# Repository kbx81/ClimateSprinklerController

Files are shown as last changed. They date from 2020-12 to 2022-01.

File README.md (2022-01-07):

# kbx's Climate and Sprinkler Controller

Climate and Sprinkler Controller
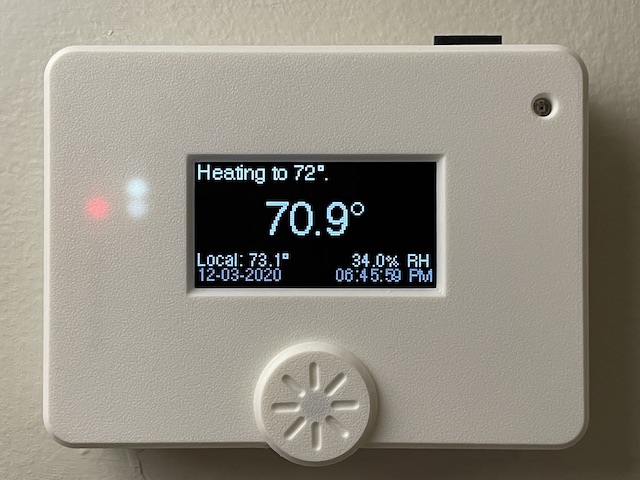
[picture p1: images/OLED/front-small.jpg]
Climate and Sprinkler Controller Climate and Sprinkler Controller - OLED


## A DIY Thermostat and/or Sprinkler (Valve) Controller

Here you'll find plans for an ESP32-based controller designed with [ESPHome](https://esphome.io) in mind. It is primarily designed for switching 24-volt AC circuits but it is flexible by design and should be adaptable to other types of electrical workloads.

In the [Preface](PREFACE.md) you will find background information about this project such as how it came to be and some personal thoughts and experiences I've had with home automation through the years.

In the [Hardware](HARDWARE.md) document you will find a general explanation of the theory of operation of a thermostat as well as a design overview of this device, some handy tips (should you choose to build one), construction, usage, and installation detail.

Finally, the [Hardware Detail](HARDWARE_DETAIL.md) document aims to explain why I did what I did -- design decisions, etc.

## Design Versions

At present there are two major "versions" of (iterations on?) the device -- a version that supports an OLED display such as the [SSD1325](https://www.adafruit.com/product/2674) and a version (well, actually three versions) that supports a Nextion touchscreen display. The project files for each can be found in its respective directory:
 - OLED versions:
   - [Version 2 (WROOM)](WROOM/)
   - [Version 3 (WROVER)](WROVER/)
 - Nextion versions:
   - [Nextion 3.5"](WROVER-Nextion3.5/) (contains no switching hardware!)
   - [Nextion 5"](WROVER-Nextion5/)
   - [Nextion 7"](WROVER-Nextion7/)

## PCB and BoMs

The schematic and PCB were drawn in [KiCAD](https://www.kicad.org). I had PCBs fabricated by [Elecrow](https://www.elecrow.com) but nearly any PCB fabricator should be able to manufacture these without any issues.

On [Octopart](https://octopart.com) I have posted a bill of materials (BoM) for each design version:
 - OLED versions:
   - [Version 2 (WROOM)](https://octopart.com/bom-tool/XvGbAePy)
   - [Version 3 (WROVER)](https://octopart.com/bom-tool/vZKpLnMD)
 - Nextion versions:
   - [Nextion 3.5"](https://octopart.com/bom-tool/dj6BW0gV) (contains no switching hardware!)
   - [Nextion 5"](https://octopart.com/bom-tool/kHZhyfjO)
   - [Nextion 7"](https://octopart.com/bom-tool/b5Lb00Zs)

### Important!

**Save money** by reading through the [build guide](HARDWARE.md) **before** you order any parts, as you likely _do not need **every** part in the linked BoMs!_ (For example, there are footprints multiple sensors on each PCB. You do not need all of the sensors!)

## ESPHome Configuration & Code

I've created a separate repository for my [ESPHome](https://esphome.io) [configurations](https://github.com/kbx81/esphome-configs); if you're looking for a starting point/example configuration, please have a look there.

## Legal stuff and License

Everything you see here is provided to you free of charge. You are free to use it however you please within the constraints of the license -- but you do so at your own risk. I accept absolutely no liability if you cause damage to your property, HVAC system, or any other hardware you choose to connect to this device.

The circuit schematics, PCBs and enclosures found here are licensed under the [Creative Commons Attribution-ShareAlike 4.0 International License](http://creativecommons.org/licenses/by-sa/4.0/).



_Thanks for visiting!_

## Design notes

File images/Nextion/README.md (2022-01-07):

# kbx's Climate and Sprinkler Controller

## Photo Gallery

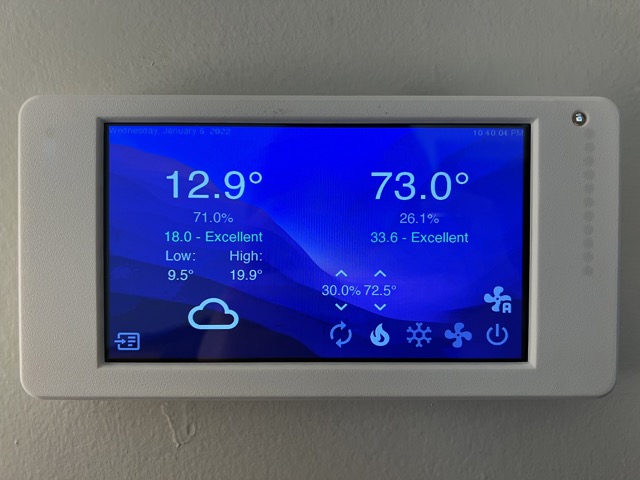
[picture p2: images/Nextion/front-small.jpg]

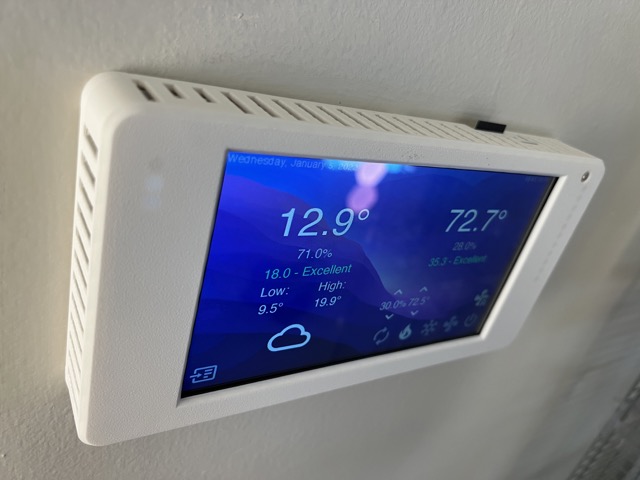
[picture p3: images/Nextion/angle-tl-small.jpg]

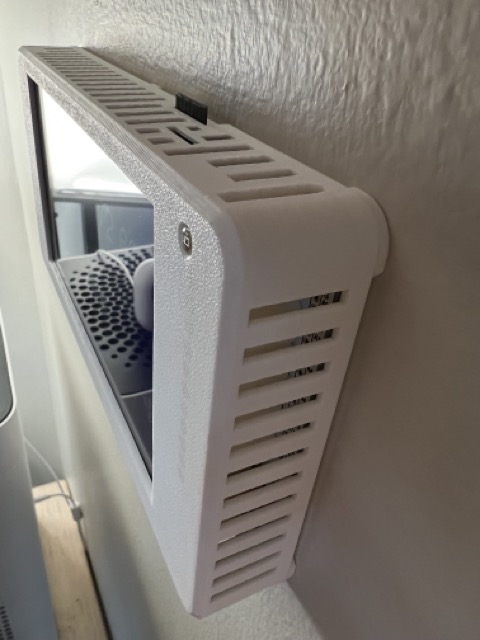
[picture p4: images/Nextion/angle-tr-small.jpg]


## Legal stuff and License

Everything you see here is provided to you free of charge. You are free to use it however you please within the constraints of the license -- but you do so at your own risk. I accept absolutely no liability if you cause damage to your property, HVAC system, or any other hardware you choose to connect to this device.

The circuit schematics, PCBs and enclosures found here are licensed under the
 [Creative Commons Attribution-ShareAlike 4.0 International License](http://creativecommons.org/licenses/by-sa/4.0/).



_Thanks for visiting!_

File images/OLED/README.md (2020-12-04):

# kbx's Climate and Sprinkler Controller

## Photo Gallery

Climate and Sprinkler Controller
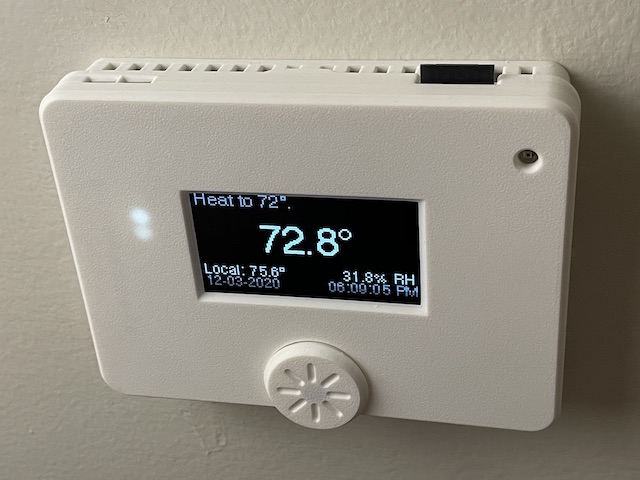
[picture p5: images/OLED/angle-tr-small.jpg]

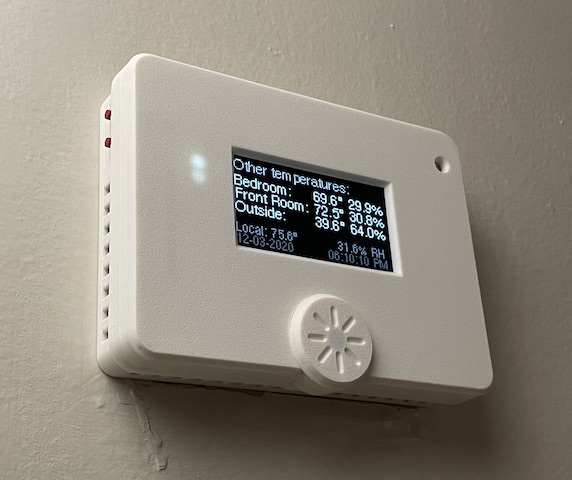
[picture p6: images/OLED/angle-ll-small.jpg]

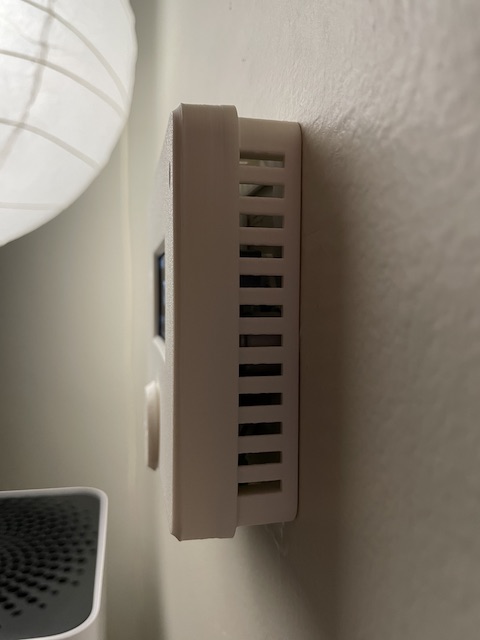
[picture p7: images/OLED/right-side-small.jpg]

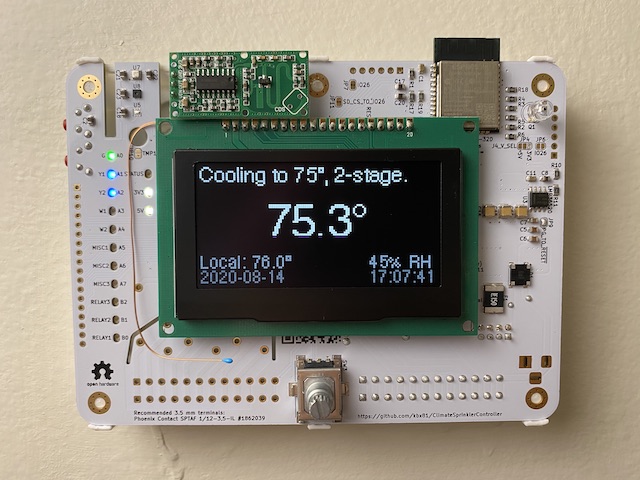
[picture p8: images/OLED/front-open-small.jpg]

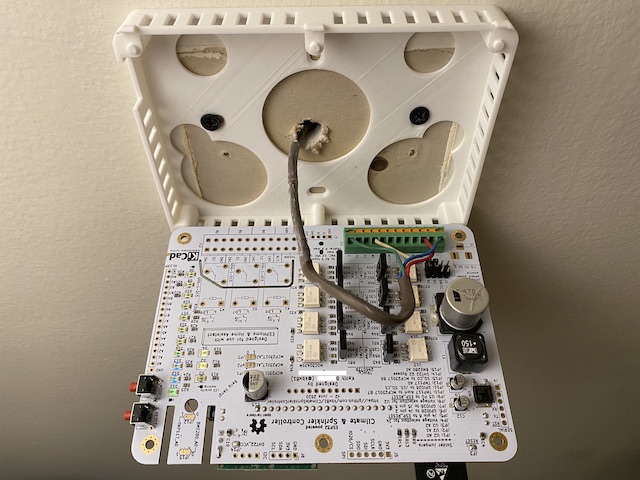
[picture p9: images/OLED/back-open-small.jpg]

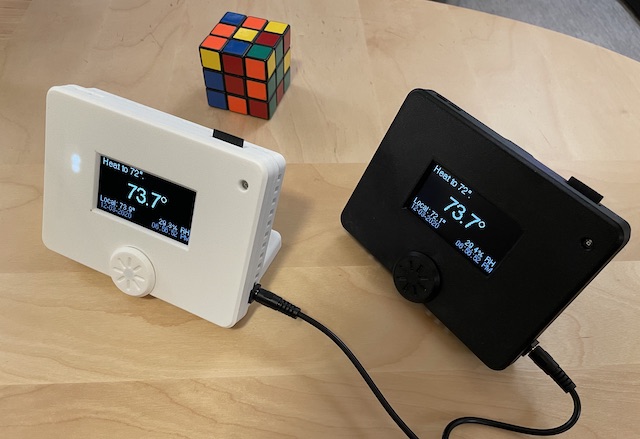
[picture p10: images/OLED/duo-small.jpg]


## Legal stuff and License

Everything you see here is provided to you free of charge. You are free to use it however you please within the constraints of the license -- but you do so at your own risk. I accept absolutely no liability if you cause damage to your property, HVAC system, or any other hardware you choose to connect to this device.

The circuit schematics, PCBs and enclosures found here are licensed under the
 [Creative Commons Attribution-ShareAlike 4.0 International License](http://creativecommons.org/licenses/by-sa/4.0/).



_Thanks for visiting!_

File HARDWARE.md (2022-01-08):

# kbx's Climate and Sprinkler Controller

Climate and Sprinkler Controller
Climate and Sprinkler Controller Climate and Sprinkler Controller - OLED

**If you want to dive right in to prepare your own build, skip down to the [Design Overview](#Design-Overview) section.**

This project started as a thermostat, but, application aside, it's just a processor with some combination of switches, sensors and/or a display connected to it. There are footprints on the PCBs for up to eleven switches and up to six sensors. It's primarily aimed at controlling 24 volt AC loads, although its relay(s) will allow switching a range DC voltages if required. Therefore, it should be able to operate more or less anything over a reasonably wide range of voltages and currents, from HVAC systems to electric sprinkler valves to security system hardware and variety of other things.

## The Basics

**If you are not planning to use this as a thermostat and/or are already familiar with HVAC system control and wiring, skip to the next section.**

### What is a Thermostat?

A thermostat is a switch. It is a switch that happens to be controlled by temperature. The switch is either on or it is off.

Yup. That's it. It's literally just a temperature controlled switch -- I'm not over-simplifying. That's really all it is.

If your thermostat happens to control your heating system, it does exactly two things:
 1. When the temperature drops below the temperature you set on it, the switch turns on.
 1. When the temperature rises above the temperature you set on it, the switch turns off.

You thought it was more complicated than that? Sorry if I've disappointed you! That's really about it. Don't believe me? Here's a [lovely video](https://youtu.be/ZZC0SP02PqY) if you'd like a closer look!

Ok, ok..._some modern systems_ allow control that is more advanced than just that. Still, it's reasonably safe to say that most (residential) systems that are either more than about ten years old or are "small" (for example, those found in single or two bedroom homes/apartments that just don't require a lot of power to heat or cool them) do little more than that. For larger homes or (commercial) buildings, the control may be more complex and, as such, may require a more complex controller. Those are probably out of the scope of what's here.

### Getting Connected

I'm not going to reinvent the wheel here. There are a number of guides that explain [thermostat wiring](https://lmgtfy.com/?q=thermostat+wiring) if you are interested in learning more. Where I live, forced-air systems that both heat and cool are most common and, as such, most of my experience is with them. To quickly summarize, our thermostats are usually connected to these systems with four to five wires:
 - `R`: a red wire, which is "live" with 24 volts AC
 - `G`: a green wire, which controls the system's main blower fan. The thermostat internally shorts this to the `R` wire to activate the fan.
 - `W`: a white wire, which controls the system's heating capability. The thermostat internally shorts this to the `R` wire to activate heating.
 - `Y`: a yellow wire, which controls the system's cooling capability. The thermostat internally shorts this to the `R` wire to activate cooling.
 - `C`: a blue wire, which provides the return path from the `R` wire (above) to complete the (24 volt AC) circuit. **This is the wire that is usually missing and brings about the "not enough wires" problem I described in the [Preface](PREFACE.md).** Without this wire, there is no reliable way for the thermostat to draw power from the system and consequently it will not work because it simply has no power. This is the reason thermostats with batteries in them are so common here now -- their old mechanical predecessors simply didn't require power to function as modern, electronic thermostats do. As a cost-saving measure, installers often ran cables that did not include this wire.

### Even More Connected

More modern systems may have additional wires, such as a `W2` (second stage heating), `Y2` (second stage cooling), `RH` (`R` for heating system), or `RC` (`R` for cooling system). These are arguably only found in large(r) homes or buildings where extra cooling or heating capacity might be needed to adjust the indoor temperature when the outdoor temperature is more extreme. Still, the controller you've found here can support these particular connections (and then some) if they are available!

In addition to heating and cooling, some systems have the ability to humidify and/or dehumidify. Here, it is common to use the air conditioning system for dehumidification, while humidification is accomplished with a separate unit when needed (typically in the winter season). If available, you can connect (de)humidifiers to any of this controller's relays or "MISCx" TRIACs -- confirm the unit's power requirements before doing so!

## Design Overview

When I design devices such as this, I tend to focus on flexibility -- cost is usually an afterthought. This device is no exception; it can be built at least three different ways...but probably isn't the cheapest possible DIY option.

There are five key components:
 - Power supply
 - Processor (ESP32)
 - Sensors
 - Display
 - I/O Expander and switching hardware:
   - TRIACs, opto-isolators, snubber circuits
   - Relays, FETs, kick-back diodes

I can probably go without saying that the power supply and processor are always required if you want it to function at all. While (the) sensor(s) may be omitted, this is not recommended if it is to be used as a climate control device (I'll explain why later). With these items in mind, it is otherwise possible to omit:
 - the display, or
 - the I/O expander and switching hardware

Any combination of TRIACs and/or relays may be installed; in other words, it is not necessary to install _all_ relays and/or _all_ TRIACs. Just install the number of TRIACs and/or relays that you need for your use case. For example, if the application requires a single DC circuit and two AC circuits, only a single relay and two TRIACs could be installed. As an alternative in this situation, three relays could be used (and no TRIACs). This is entirely at the discretion of the builder. (Note that a benefit of the TRIACs is that they are not subject to contact wear as relays are -- in theory, they should last forever. Relay contacts wear out and will stop working after some time.)

Based on the above two build configurations, I've come to think of these devices in two ways:
 - A `controller`, which is a unit that has the switching hardware and may or may not have a display and encoder
 - A `satellite`, which has a display and encoder but no switching hardware

Both build configurations have at least one sensor.

I use a couple `satellite` units to monitor and report to Home Assistant the temperature in remote (with respect to the wired-in `controller` build) rooms. This data can then be used to guide the `controller` that is physically connected to the HVAC system. It's easy to aggregate the data from any number of `satellite` units and, with the right automations in place, use it to control the system. In addition, `satellite` units can provide alternate points of control for the system; for example, put one next to your bed and you could adjust the temperature without using your smartphone or voice control (and potentially waking up your SO in the process).

`Controller` units are builds that have (some) switching hardware but may or may not have a display. If built with a display, you can probably mount it on the wall as a direct replacement for your existing thermostat. With no display, the controller can still control your HVAC system (or whatever else you've wired up to it), you just won't be able to interact with it locally (at least, not easily). While building it this way might seem like a silly idea, _this is the solution to the "not enough wires" problem._

### Solving the "Not Enough Wires" Problem

_How does building it without a display solve the "not enough wires problem"?_

Imagine, for a moment, that your HVAC system is located in the basement of your house. Your thermostat is installed on a wall on the main floor. The cable to your thermostat from your HVAC system runs up, through the floor, around a corner, down the hall and finally up the wall to where your thermostat is mounted. You need five wires to install your new thermostat, but the system installer ran a cable that has only four wires. What do you do?

(At this point, I can assure you that your HVAC professional will install a small white plastic box with a tiny LCD on it. It will require a battery (or two) that you'll have to change periodically, probably once or twice a year. The battery will always fail at an inopportune time.)

By building one of these as a `controller` (and perhaps without a display and encoder), you can:
 1. Mount your `controller` (very) near your HVAC system -- for example, on the wall directly behind it...or hanging on the side of it
 1. Get a short cable--say, one to two yards/meters or so--that _does_ have enough wires (or you could recycle a couple pieces of the cable you'll disconnect in the next step!)
 1. Disconnect the original cable from your HVAC system to your old thermostat, then
 1. Connect the new short cable from your HVAC system to the new `controller` that's now right next to your system.

What you have now is a switching device that can still _tell your HVAC system what to do_ -- you'll just need to feed it data from remote sensors (in this example, sensors that are located upstairs). These remote sensors could be the "satellite" units I described above -- or they could be something even more simple, such as [these sensor boards](https://github.com/kbx81/TempHumSensWithESP01). There also exists a super cheap [DHT22 + ESP-01 module](https://www.amazon.com/gp/product/B07L6CYFT9/)...although, in practice, I _really_ don't recommend DHT modules for this application -- they're too inconsistent. It's up to you!

So, to summarize:
 - The `controller` is installed (very) near your HVAC system and is connected to it with a short, easily-installed cable that _has enough wires_.
 - `Satellite` sensors located in areas to be climate controlled report data to Home Assistant.
 - (An) automation(s) in Home Assistant parse and feed this data back to the `controller` so that it can control your system as appropriate.

Ok, ok...I admit, it's more of a workaround than a "real solution". Even so, it works great!

### But What If...

I'm going to assume that, since you're here and are reading this, you're at least somewhat technically inclined and are asking "What if my Home Assistant goes down??? What if my Wi-Fi goes down??? This won't work then so I can't use it!" You may recall that, above, I stated: "While (the) sensor(s) may be omitted, this is not recommended if it is to be used as a climate control device." In the [ESPHome](https://esphome.io) [configuration](https://github.com/kbx81/esphome-configs/blob/master/CSC.md) that I built for my devices, two events are monitored:
 1. The API connection state (Am I connected to [Home Assistant](https://www.home-assistant.io)?)
 1. The time since the [ESPHome](https://esphome.io) [template sensor](https://esphome.io/components/sensor/template.html) was last updated (by (an automation in) [Home Assistant](https://www.home-assistant.io))

There is a timer for each of these two events; each event's respective timer is reset each time the event occurs (such a mechanism is also often called a "watchdog"). If the device either 1. loses its connection to the [Home Assistant](https://www.home-assistant.io) API ([Home Assistant](https://www.home-assistant.io) is down, Wi-Fi is down) or 2. does not receive an update to the [template sensor](https://esphome.io/components/sensor/template.html) (your automation that updates it broke or otherwise stopped running), after a duration of your choosing, it will stop using the [template sensor](https://esphome.io/components/sensor/template.html) and switch to using its local sensor (BME280/BME680/SHTC3/TMP117/DHT22/Thermistor...note that in my [configurations](https://github.com/kbx81/esphome-configs/blob/master/CSC.md) I revert to using the BME680 in this case). While the data from its local sensor(s) won't necessarily be consistent with the sensors located in the areas of interest, it _will_ provide the controller with _some_ data so that it can continue to function on some level. It may not be ideal, but it can keep the system from becoming totally useless (and, as such, your house doesn't freeze/turn into a sauna).

It's not a perfect solution to the original problem and I'm sure that it won't work for everybody. Still, it should offer a level of flexibility that I think many home automation enthusiasts can work with. My experience has proven that [Home Assistant](https://www.home-assistant.io), [ESPHome](https://esphome.io) and my Wi-Fi/home network are extremely reliable and that they can handle this task with no trouble at all. They break _only when I break them_.

## I Want (to Build) One

Awesome! Read on for build-related information, tips, etc.

### Before You Build

If you've read through the previous section, you may have already begun thinking about how you'd like to build yours. _But,_ just in case you skipped that part, I'll outline the key points you need to consider here:
 1. How many units do you need? Are you simply replacing a single existing thermostat or do you desire/plan to extend the capabilities of your system, as well?
 1. How many control channels do you need for your intended application? For example, if you're only controlling a heating system, you likely only need a single channel. If you have a more complex system that can (for example) heat, cool, fan and humidify, you need at least four channels/circuits. This determines how many TRIACs and/or relays you will need.
 1. If you are replacing an existing thermostat, _do you have enough wires?_ (My favorite problem!) If not, you may want to build a `controller` version as well as a `satellite` version (see above). As an alternative, you could build a complete version and power it with an external source through the barrel jack on the side. I recommended _not_ installing the barrel jack if your HVAC system will provide power through the `R` and `C` wires.
 1. Which sensor(s) do you wish to use? Are you comfortable soldering tiny parts such as the BME280, BME680, SHTC3 or TMP117 (you need a hot air station or (toaster) oven for these!)? If not, is a DHT22 or thermistor accurate/consistent enough for your liking/needs? If not, consider a BME280, BME680, SHTC3 or TMP117 module from [Adafruit](https://www.adafruit.com/product/2652) or [Sparkfun](https://www.sparkfun.com/products/13676)! They can be plugged into one of the headers along the edges of the board. (My personal favorite is the BME680.)
 1. Do you want/need a display? If so, which display do you want to use? On the v2 and v3 boards there are headers for two different displays -- the [SSD1325](https://www.adafruit.com/product/2674) (grayscale, big) and the [SSD1351](https://www.adafruit.com/product/1431) (color, not big). If you prefer a touchscreen, there are three different boards to match three different Nextion display sizes. I highly recommend the [Intelligent series](https://nextion.tech/intelligent-series-introduction/) or, as a less-expensive alternative, the [Enhanced series](https://nextion.tech/enhanced-series-introduction/). (I'd avoid the Basic series altogether -- they're rather sluggish.) My personal favorites are the Intelligent series models `NX8048P070-011C` (7") or the `NX8048P050-011C` (5"); I've also built [HMI configurations](https://github.com/kbx81/esphome-configs/tree/master/nextion/CSC/climate) for the Enhanced series `NX4832K035` (3.5"), `NX8048K050` (5"), and `NX8048K070` (7"). **Note that the 3.5" board does not include any switching hardware -- as such, it can only function as a satellite.**
 1. Do you want the display to be motion-activated? This is especially important if it is an OLED-type of display -- they have a relatively short lifespan and can burn in! I used an [RCWL-0516 module](https://www.amazon.com/gp/product/B07MTWZDQZ/) to accomplish this, although a PIR sensor is suitable, as well. There is a header on each board for this purpose. (Pro-tip: I've installed a short jumper cable with a dupont-style connector and mounted the [RCWL-0516 module](https://www.amazon.com/gp/product/B07MTWZDQZ/) into the back side of the front cover of the enclosure. This arrangement distances it from the PCB which allows it to function more reliably.)

Once you have the PCBs and parts in-hand, you're ready to begin building!

### Construction

The bill of materials (BoM) for each version of the board contains not only the list of parts, but also the component references -- it can be used to determine what parts go where on the PCB. This (as well as some patience and a steady hand) should be everything you need to complete assembly.

Note that the PCB is designed in a way that it has parts on both sides. Examine it carefully and **observe that one side has only small parts** while the other side has several larger parts. **I highly recommend starting with the side of the board that has only small parts on it.** This side has no "heavy" or otherwise particularly large parts on it, so assembling it first will make assembling the side with the larger parts later on much easier. I use and recommend a stencil with solder paste and a hot air soldering station, so having a board that doesn't wobble (much) when it's on the desk is important.

As you're assembling, you'll notice a number of solder jumpers on the board. This is a good point to discuss what they do so you can determine which ones you should bridge and how.

#### Solder Jumpers: v2/WROOM

- JP1 to JP3: U2 (MCP23017) I2C address selection. These are used to modify the I2C address of the MCP23017. (*See the note below.)
- JP4: Voltage selection for pin 3 of J4. Not connected by default; create a solder bridge to the voltage of your choosing if connecting an external device. **Not required for ESP32 programming.**
- JP5: J4 pin 6 to ~ESP_RESET aka EN -- connects through C4 to the ~RESET aka EN line of the ESP32 to allow resetting from a connected serial adapter.
- JP6: Connects the ESP32's GPIO26 pin to J4 pin 2.
- JP7: Connects the ESP32's GPIO26 pin to J5 pin 6.
- JP8: Voltage selection for U2 (MCP23017). This IC can operate with either 3.3 or 5 volts. _Use 5 volts with caution_ as the interrupt lines may put 5 volts onto the ESP32's GPIO 36 and/or 39 pins! This may cause undefined behavior and/or damage the ESP32. If using 5 volts, these pins must be configured to open drain mode on the MCP23017.
- JP9: U3 (LMR36520) PG to ~ESP_RESET aka EN -- allows the LMR36520 to hold the ESP32 in "reset" state until the power from the buck converter has stabilized.
- JP10: TMP117 Alert to MCP23017 B7. Not used if the TMP117 is not installed.
- JP11: ESP32 GPIO26 to J10, SD_CS pin -- may be used if the [SSD1351](https://www.adafruit.com/product/1431) is installed and the SD card is to be used.
- JP12: TMP117 A0 -- allows changing the I2C address of the TMP117. (*See the note below.)
- JP13: SD_CD to MCP23017 B6 pin -- may be used if the [SSD1351](https://www.adafruit.com/product/1431) is installed and the SD card is to be used.
- JP14: DHT22 Q2 Bypass. Shorts the drain and source pins of Q2. This transistor can be used to power-cycle the DHT22 if required by the application (they sometimes stop responding). Not used if the DHT22 is not installed. Note that this transistor could also be used to drive an LED, if required.
- JP15: BME280 A0 -- allows changing the I2C address of the BME280. (*See the note below.)

#### Solder Jumpers: v3/WROVER

- JP1 to JP3: U2 (MCP23017) I2C address selection. These are used to modify the I2C address of the MCP23017. (*See the note below.)
- JP4: MCP23017 Interrupt B output to GPI39
- JP5: MCP23017 Interrupt A output to GPI36
- JP6: Voltage selection for pin 3 of J4. Not connected by default; create a solder bridge to the voltage of your choosing if connecting an external device. **Not required for ESP32 programming.**
- JP7: J4 pin 6 to ~ESP_RESET aka EN -- connects through C4 to the ~RESET aka EN line of the ESP32 to allow resetting from a connected serial adapter.
- JP8: Connects the ESP32's GPIO26 pin to J4 pin 2.
- JP9: Connects the ESP32's GPIO26 pin to J5 pin 6.
- JP10: Voltage selection for U2 (MCP23017). This IC can operate with either 3.3 or 5 volts. _Use 5 volts with caution_ as the interrupt lines may put 5 volts onto the ESP32's GPIO 36 and/or 39 pins! This may cause undefined behavior and/or damage the ESP32. If using 5 volts, these pins must be configured to open drain mode on the MCP23017.
- JP11: U3 (LMR36520) PG to ~ESP_RESET aka EN -- allows the LMR36520 to hold the ESP32 in "reset" state until the power from the buck converter has stabilized.
- JP12: TMP117 Alert to MCP23017 B7. Not used if the TMP117 is not installed.
- JP13: ESP32 GPIO26 to J10, SD_CS pin -- may be used if the [SSD1351](https://www.adafruit.com/product/1431) is installed and the SD card is to be used.
- JP14: TMP117 A0 -- allows changing the I2C address of the TMP117. (*See the note below.)
- JP15: SD_CD to MCP23017 B6 pin -- may be used if the [SSD1351](https://www.adafruit.com/product/1431) is installed and the SD card is to be used.
- JP16: BME280 A0 -- allows changing the I2C address of the BME280. (*See the note below.)

#### Solder Jumpers: Nextion 5" and 7"

- JP1 to JP3: U2 (MCP23017) I2C address selection. These are used to modify the I2C address of the MCP23017. (*See the note below.)
- JP4: MCP23017 Interrupt B output to GPI39
- JP5: MCP23017 Interrupt A output to GPI36
- JP6: Nextion power switch (U4) bypass
- JP7: Voltage selection for U2 (MCP23017). This IC can operate with either 3.3 or 5 volts. _Use 5 volts with caution_ as the interrupt lines may put 5 volts onto the ESP32's GPIO 36 and/or 39 pins! This may cause undefined behavior and/or damage the ESP32. If using 5 volts, these pins must be configured to open drain mode on the MCP23017.
- JP8: GPIO26/~RTS~ to J5 pin 2
- JP9: Voltage selection for J5
- JP10: U5 (LMR36520) PG to ~ESP_RESET aka EN -- allows the LMR36520 to hold the ESP32 in "reset" state until the power from the buck converter has stabilized. **Do not connect if powering from USB.**
- JP11: Auto-reset to ESP32 EN (allows the FT232 to reset ESP32)
- JP12: Auto-reset to ESP32 GPIO0 (allows the FT232 to invoke the ESP32's bootloader as required)
- JP13: GPIO15 to J6 pin 6 (to be used as SPI CS)
- JP14: BME680 A0 (*See the note below.)
- JP15: BME280 A0 (*See the note below.)
- JP16: TMP117 Alert to MCP23017 B7
- JP17: TMP117 A0 (*See the note below.)

#### Solder Jumpers: Nextion 3.5"

- JP1: GPIO26/~RTS~ to J4 pin 2
- JP2: Voltage selection for J4
- JP3: GPIO15 to J5 pin 6 (to be used as SPI CS)
- JP4: U3 (LMR36520) PG to ~ESP_RESET aka EN -- allows the LMR36520 to hold the ESP32 in "reset" state until the power from the buck converter has stabilized. **Do not connect if powering from USB.**
- JP5: VCC selection -- connects VCC to buck converter output or directly to barrel connector (J2)
- JP6: Auto-reset to ESP32 EN (allows the FT232 to reset ESP32)
- JP7: Auto-reset to ESP32 GPIO0 (allows the FT232 to invoke the ESP32's bootloader as required)
- JP8: Nextion power switch (U4) bypass
- JP9: TMP117 Alert to GPI36
- JP10: TMP117 A0 (*See the note below.)
- JP11: BME680 A0 (*See the note below.)
- JP12: BME280 A0 (*See the note below.)

*Note: This jumper is shorted to `0` by default; if you wish to modify it, use a razor knife to cut the trace between the center and `0` pads on the board and then create a solder bridge between the center pad and the `1` pad. Use your DMM to confirm proper/expected conductivity!

After you're done assembling but **before powering it on for the first time**, always check for shorts -- particularly across power tracks. I use my DMM to measure between ground, the 3.3 volt and 5 volt rails to be sure they are not shorted together. If any of them are, you'll need to carefully check your soldering work and look for solder bridges. If there are no shorts, it's probably safe to power it on and load the firmware image onto the ESP32.

#### One More Thing!

There is a header labeled `POWER SEL` (either `J2` or `J3`) to the lower left of the PCB. This header **must** be fitted with a jumper to select where the board should draw power from. There are up to four options: one of three possible AC circuits (`RC`/`C`, `RH`/`C`, or `RMISC`/`C`) as well as the barrel jack (`J1` or `J2`). In the event that your HVAC system does not have separate/individual `RC` and/or `RH` wires, it is possible to jumper them together by placing jumpers on _both_ `RC` _and_ `RH`. This effectively turns them into a single `R` terminal. `RMISC` may also be added into this mix, as needed. This may be done if only a single `R` wire is available/connected.

Note that on all except the Nextion 3.5" board the barrel jack may be an AC or DC source and it is not polarity sensitive because of the bridge rectifier. It must provide a minimum of 7.5 volts and a maximum of 40 volts DC or 30 volts AC (because RMS, yada yada). A common 12-volt DC power brick will likely work best if the board is to be powered this way. Depending on the input voltage and connected peripherals/accessories, its current requirement will vary. Even with a low input voltage (say, nine volts or so) it shouldn't need more than about 250 mA unless you've attached some extra hardware (sensors, LEDs, etc.) -- keep in mind, however, that the Nextion versions are slightly more power-hungry, depending on the display size. Even so, because of the buck converter, a higher voltage source will mean a lower current draw. Ideally the rating of the polyfuse `F1` should be adjusted accordingly, although the specified value should be suitable for most situations.

**Note that if, on the Nextion 3.5" board, `JP5` is set to bypass the buck converter, _only_ a 5-volt DC source may be used!**

For safety reasons, do not connect more than one power source at a time.

### Initial Firmware Flashing

After confirming that your new boards are electrically safe to power on (you checked everything as I suggested above, right?!), the ESP32 needs to have [ESPHome](https://esphome.io) installed ("flashed") onto it.

You'll need to either build an [ESPHome](https://esphome.io) configuration of your own or [start with mine](https://github.com/kbx81/esphome-configs/blob/master/CSC.md) and tweak them to your liking.

The Nextion versions of the boards have an FT232 USB-to-serial IC on the board; I definitely recommended using this for installing the firmware. Bridge both of the "Auto-reset" jumpers on these boards for the best experience.

If you're not using one of the Nextion versions of the boards or you did not place the FT232, you'll need to manually invoke the ESP32's bootloader to enable flashing. Hold down the "Mode" pushbutton (which is connected to the ESP32's GPIO 0 pin) as you either power it on or tap the adjacent reset button, then release the "Mode" button. With the bootloader invoked, you can use the pin header labeled "SERIAL" (`J4` or `J5`) to connect your serial adapter and flash the ESP32. There are plenty of guides on flashing ESP32s out on the web, so I'm not going to reinvent the wheel here. If you are having difficulty doing so, however, use your DMM and check for shorts across the transmit (TX) and receive (RX) lines. It's possible one or the other is shorted to ground, Vcc, or another adjacent pin or track. In some cases, it may be necessary to hold down the encoder button (connected to GPIO 2) _as well as_ the "Mode" button (GPIO 0) to properly invoke the bootloader -- try this first if you're having any trouble.

Once you've installed the firmware onto the ESP32, you're ready to begin using your Climate and Sprinkler Controller(s)! If you made it this far, nice work!

## Installation and Usage

Physically installing the controller is pretty straight forward -- the terminal strips are labeled just like a typical thermostat. _Power off your HVAC system before (dis)connecting anything!_ Connect the wires as you would any other thermostat and you should be ready to go. The [ESPHome](https://esphome.io) [configurations](https://github.com/kbx81/esphome-configs/blob/master/CSC.md) I've created aim to function just like a "real thermostat".

Once all the little wires are connected, turn your HVAC system's power back on and your new controller should start up. Please see [this document](https://github.com/kbx81/esphome-configs/blob/master/CSC.md#thermostat-user-interface-ui) for an explanation of the device's user-interface (UI).

To test the thermostat:

- If your system supports heating, set the thermostat mode to either `Auto` or `Heat` mode and turn the temperature up to a value at least one degree above the currently displayed room/air temperature. Heating should commence.
- If your system supports cooling, set the thermostat mode to either `Auto` or `Cool` mode and turn the temperature down to a value at least one degree below the currently displayed room/air temperature. Cooling should commence.

### Important Note!

The [ESPHome](https://esphome.io) [configurations](https://github.com/kbx81/esphome-configs/blob/master/CSC.md) I've created use the [thermostat's](https://esphome.io/components/climate/thermostat.html) delay timers to prevent the physical outputs (TRIACs, in this case) from changing states too quickly. For example, AC compressors are sensitive to being switched on/off rapidly (this is called "short cycling"). Because of this, you may find that cooling/heating will not stop despite that the temperature has been reset to a value that triggers the "idle" state/behavior. The display (and HA) will reflect this, but the outputs won't. Don't worry -- once the timer expires, the respective output will switch off, as expected. Note that these delays may be modified by changing the configuration to your liking -- just be careful, as making them too short will shorten the life of or even damage your system!

If all this works, you have a new thermostat! Nice work!

## Legal stuff and License

Everything you see here is provided to you free of charge. You are free to use it however you please within the constraints of the license -- but you do so at your own risk. I accept absolutely no liability if you cause damage to your property, HVAC system, or any other hardware you choose to connect to this device.

The circuit schematics, PCBs and enclosures found here are licensed under the
 [Creative Commons Attribution-ShareAlike 4.0 International License](http://creativecommons.org/licenses/by-sa/4.0/).



_Happy building!_

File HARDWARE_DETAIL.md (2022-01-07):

# kbx's Climate and Sprinkler Controller

Climate and Sprinkler Controller
Climate and Sprinkler Controller Climate and Sprinkler Controller - OLED

This document is for folks who want a closer look at the design of the Climate and Sprinkler Controller electronics...or want to know why I did a thing the way I did the thing.

## Design Principals

I'll say it first: I did not design this to be an Ecobee or a Nest. Instead, it is intended to be a nod towards makers to help them get to where they want to be. As such, it is designed and intended to be:
 - Flexible
 - Expandable
 - Hackable

It is not:
 - Cost optimized
 - Electrically optimized
 - Designed to do one very-specific thing

While I think it would be very cool to mass-produce these and have them available on some site like [Tindie](https://www.tindie.com), I probably don't have the time or ambition right now to do that on my own -- and I also realize that these aren't really optimized for that purpose. For that to be really successful, I think many of the aspects I mentioned above would need to be trimmed out to simplify assembly and (consequently) reduce cost. On some level, I feel like that would defeat the purpose of the original design. Everybody always wants stuff to be cheaper but, to have really nice and easy-to-work-with things, it's really difficult to do that, at least on a small (in terms of production) scale.

## Hardware Overview

There are five key components:
 - Power supply
 - Processor (ESP32)
 - Sensors
 - Display
 - I/O Expander and switching hardware:
   - TRIACs, opto-isolators, snubber circuits
   - Relays, FETs, kick-back diodes

Let's dig in and take a closer look at each one.

### Power Supply

This is a buck converter based on the TI `LMR36520` step-down converter IC. The design (and, largely, physical layout on the PCB) came directly from TI's Webench app. As arranged here, it should be capable of providing up to two amps of current at five volts. **Two amps???** Yes, I did that -- it's overkill, I know. Perhaps someday I'll scale it back so as to eliminate the huge inductor that's a part of the converter. Still, in this configuration, it should be more than capable of powering any add-ons you might wish to attach to this board. You'll find that's a common theme here -- I've considered that anyone using this will want to "hack" it and make their own changes and/or additions. As such, the buck converter here is oversized so that you can play as you wish. :)

Before the buck converter there is also a bridge rectifier and (big) smoothing capacitor. Not much else to see here...move along, please.

### Processor

The ESP32 (module) is my go-to for these projects. They are an order of magnitude better than the ESP8266 in terms of available peripherals, memory and processing power. I strongly encourage anybody and everybody to use them in their projects, too -- they're far more flexible and just generally easier to use as a result.

### Sensors

I'm often asked "why so many sensors?" The answer is simple: Physically, they are tiny and the cost associated with placing the footprints onto the PCB for each of them is, at very most, negligible. In addition, given the current situation in 2021/2022 as it relates to parts shortages, having the extra footprints allows you to use _whatever you can get_ as opposed to being locked into a specific part. Because they all use the I2C bus, you can use as many or as few as you like. If you want to go the least-expensive route, just get the cheapest one you can. If you love data and cost isn't an issue, buy them all! If you can't get your first choice because of shortages, you can use your second choice until your preferred sensor arrives. Flexibility is pretty great, yeah?

In terms of why I picked the specific sensors I picked, it more or less comes down to that these are the most well-known, well-supported and easily available (at least, prior to 2021). There isn't really a technical reason for the selection -- temperature is really the only data point they _need_ to provide. If there is a different sensor you'd like to use, the break-out headers along the edges of the boards should make it easy for you to connect it, whether it's I2C, SPI, serial or some other protocol.

### Display

I picked the OLED displays because of their great contrast. Even though they're relatively low-resolution, I like how they look and they're pretty easy to use. I just really wish I could get a _color_ OLED display that's the physical dimensions of the [SSD1325](https://www.adafruit.com/product/2674) -- it would look sooo much cooler.

After I'd created the v2/v3 PCBs, naturally a few people came back and asked, "Why not a touchscreen?!?" This brought about the Nextion versions of these.

So. Let's talk about these Nextion displays for a moment. I'll just say it: I really do not love the Nextion platform. Their editor...works...but (in my opinion) it is a hot mess; there's no integration with source control so maintaining different versions of things and tracking changes is basically impossible. I hate that only a Windows version of the editor is available. Finally, the Nextion hardware itself...well, I guess it fills a gap, but...it's 2022...touchscreen hardware like this _should be_ sooooo much better. The "Intelligent" series is the only series that I feel like I can work with. Many of the UI elements they offer (slider controls, for example) are _terribly ugly_ and not something I would _ever_ use in a modern UI. (This is primarily why my UI has up/down arrows and not a slider!) Animations/effects are choppy (low FPS) even with few elements on the display. The overall experience feels worse than using a PC running Windows 3.11 from 1993. I don't expect them to work like an iPhone but..._come on._ Lots of improvements need to be made here. In any event, I'm excited to see a couple of other projects brewing that will bring about a more powerful and more customizable display experience. I'm excited to see what the future will bring!

### I/O Expander and Switching Hardware

These components are the parts that give the software physical control of the HVAC system or sprinkler valves (or whatever else you've connected to it). There are some technical reasons for their selection. I'll explain...

First, let's talk about the `MCP23017` I/O expander. The ESP32 arguably has enough GPIO pins...why use an I/O expander? There are multiple reasons:
 - The I/O expander's pins will retain their state when the ESP32 resets.
 - Several of the ESP32's GPIO pins get bumped into undesirable states when it resets.
 - The I/O expander frees up pins on the ESP32 for other uses (displays, sensors, other I/O, etc.).

For HVAC applications, it is _very important_ that control signals are stable, consistent and don't change states too quickly. Generally speaking, the `MCP23017` physically prevents this from happening because its pins are incapable of being in a state other than "on" or "off" (and by this I mean there aren't a bunch of on-board peripherals that can be (accidentally) mapped to pins, causing (for example) a PWM signal to appear on a pin. This could be disastrous to attached hardware/systems). Worst-case, the `MCP23017` has its own built-in auto-reset circuit that will force all of its pins into a safe "off" state, effectively disengaging any attached hardware. After the ESP32 resets, it will simply reinitialize the `MCP23017` and set its pins back into the desired/necessary state. So, in short, the `MCP23017` creates a physical barrier that provides a layer of protection against "dumb" things happening to any attached hardware.

Next up: TRIACs. Why use TRIACs? Quick answer: they're more reliable and have a longer lifespan than relays. Typically they are less expensive than relays, too. They're specifically designed for switching alternating current (AC) which happens to be what most HVAC systems use for their control signals. On the PCB, around the TRIACs you'll find an arrangement of resistors, capacitors and an opto-triac. These components simply allow the I/O expander to safely and reliably switch the TRIAC on and off as required.

What about the relays? I designed in relays because I had a couple of people bring up millivolt systems. The relays allow switching of things that the TRIACs can't handle. There are some (older?) gas heating systems that use no electrical power supply at all -- instead, a small current is "induced" by the heat differential created by a pilot flame and this millivolt signal is somehow sufficient to switch the rest of the system on or off. I'm not going to pretend to understand it right now (Google is your friend if you are curious) but a physical electrical contact is the only way to switch these systems. So, I added some relays, just to cover all the bases. :) A 2N7002 FET is responsible for switching each relay coil on/off and each FET is controlled by one of the I/O expander's GPIO pins.

## Wrapping Up

I think that covers the majority of what thoughts went into the hardware. If you find you have other questions about the hardware or software, please feel free to reach out! I'm happy to respond to questions or other inquiries.

## Legal stuff and License

Everything you see here is provided to you free of charge. You are free to use it however you please within the constraints of the license -- but you do so at your own risk. I accept absolutely no liability if you cause damage to your property, HVAC system, or any other hardware you choose to connect to this device.

The circuit schematics, PCBs and enclosures found here are licensed under the
 [Creative Commons Attribution-ShareAlike 4.0 International License](http://creativecommons.org/licenses/by-sa/4.0/).



_Happy building!_

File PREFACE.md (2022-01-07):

# kbx's Climate and Sprinkler Controller

Climate and Sprinkler Controller
Climate and Sprinkler Controller Climate and Sprinkler Controller - OLED

This document outlines some of the thoughts I had that went into the design of this device.

## Why?

I started this project due to frustration with the thermostats I had at the time (more on this later). It also came about due to my general dislike of the typical cloud-based thermostats that frequently replace the old round dial or the white plastic box with (tiny, gray) LCD. I don't want a "dumb" thermostat, I don't want a battery-powered thermostat, and I don't want to be at the mercy of my ISP or ABC Corp. when they decide to turn off their web service(s) because they don't want to pay for hardware/software/servers/bandwidth anymore. I was also looking for more...flexibility...than the commercial solutions provide; I'm less interested in a thermostat and more interested in a climate control _system_.

Another issue that really bothers me and that I've seen surface quite often with respect to thermostats/HVAC control is wires. "I don't have enough wires to my thermostat to use the [insert electronic (cloud) thermostat here]." As I'm writing this, it's mid-2020; we have more really great technology now than ever before. It absolutely _blows my mind_ that, in light of this, wires are an obstacle to connecting a new thermostat. Now, I'm not saying that wires are not necessary -- of course, it's got to connect to your system somehow. I get that. But why do they need to stretch across your house, through walls and floors and ceilings where you can't easily get to them?...and why on earth do you need more than two? I often see "solutions" to the "wires problem" in the form of add-on hardware you can spend extra money on...although I've also gathered that these are less than trouble-free. Or you can just concede and use a cheap mechanical option...or a battery-powered option...but then of course you'll have to swap batteries every few months, which definitely works but it is not something I'm willing to settle for. Regardless, it's quite clear that "not enough wires" is a problem lots of folks run into when installing these things. I don't know why it bothers me so much; it just seems like a problem that should have been put to rest and completely solved for everybody everywhere 20+ years ago.

As a home automation enthusiast, I've already used at least a couple different "smart" thermostats. One was an old Honeywell IAQ, which featured a basic touchscreen interface and a four-event-per-day scheduling system, which was nice, but...eh. Over time I began installing Insteon hardware all around the house and, in sticking with the platform, replaced the Honeywell thermostat with the Insteon thermostats. Yes, plural, _thermostats_. The Insteon thermostats are actually pretty cool -- there is a wired one which you connect (yes, with wires, assuming you have enough of them) directly to your HVAC system and it can "pair" with up to two wireless units which are battery-powered and, as such, are actually portable. You can take them from room to room as you like, or they can be wall-mounted. One is designated the "master" and the temperature the master reads determines what the HVAC system will do (heat, cool, etc.); the master can be changed on-the-fly with a button on the front. Set the one in your bedroom as the master while you're sleeping, then change the other to be the master during the day/evening when you're in the living room watching TV. Sounds great...but now I'll tell you that they're tragically unreliable. Specifically, the wired unit has a terrible habit of jumping to a different mode when the HVAC system starts. For example, let's pretend it's winter and you have the system set to "heat" mode. The house gets cold, the thermostat sees the temperature drop, so it turns on the heat. A few seconds after switching on the heat, the thermostat magically switches itself into "cool" mode -- so the heat promptly turns off. Sure, it's not like the AC switches on, but it's not heating. Now your house just continues to get colder. Sometimes they even change the set points for you. I keep it at 72 (low)/75 (high) degrees F, but sometimes I look and it has suddenly switched itself to 60/80. No idea where those numbers came from, but I assume they're some kind of default values it randomly loads up for reasons unknown. So...overall...neat idea, terrible implementation. Not recommended. (I solved the erratic behavior with automations in Home Assistant -- the mode/temperature changes _are_ reported, so HA would see them and correct them as needed. Hacky solution, but it works great.)

Those aside...why not just get a Nest or Ecobee? I'm just not a fan of cloud-dependent devices; you're at the mercy of the manufacturer. See also: "Works with Nest". I gather that Ecobee allows at least some local control and isn't entirely dependent on the cloud, but, even so, I had some other ideas in mind...

"What...other...ideas?" you might ask.

The ideas I had are probably best expressed as a list of requirements. That's what engineers tend work with, right? So, here's what I defined as primary objectives for this project:
 - It must be "connected" so that it may be controlled and monitored remotely
 - It must not have any dependency on "the cloud". Absolutely none. At all. Whatsoever. Period.
 - It must support at a minimum heating, cooling, and fan-only modes of operation
 - It must be extensible such that any number of additional sensors may be added to monitor the temperature in locations other than where the thermostat is physically installed
 - It must be able to _act_ on data from other sensors and, if desired, _completely ignore_ its local sensor (aka the sensor on the device)
 - It must offer a solution to the "not enough wires" problem
 - It must not require batteries
 - It must be able to be locally controlled (like, with buttons), even when in a disconnected/offline state
 - It must function regardless of its state of connectivity to other sensors and/or to its point of remote control

...and some secondary ("nice to have") objectives (some of which spin out of the primary objectives):
 - In addition to heating, cooling, and fan-only modes, it should support two-stage heating and cooling, as well as humidification and dehumidification
 - It should offer at least some support for non-24-volt AC systems, such as millivolt systems
 - It must be able to be constructed in a "headless" manner (more on this later)
 - It should have a clear, easy-to-read display and a simple human interface
 - It should be able to display readings from other, remote sensors
 - It must be able to be powered from a source other than 24 volt AC
 - It should be reasonably easy to connect and install
 - It should be able to be constructed with the minimum required parts given its use case
 - It should be reasonably maker-friendly
 - It should be self-documenting as much as possible

## The Solution

As I tend to do, I designed and built something that's arguably a bit overkill. It meets all of the design goals I listed above and then some. The result is:
 - An ESP32-WROOM-32 (v2) or ESP32-WROVER-32 (v3 and Nextion versions) module as the "brain" with an MCP23017 (I2C) I/O expander for switching the...
 - Up to 11 control channels -- up to eight opto-isolated TRIAC-based switches and up to three SPDT relays
 - Indicator LEDs for all on-board control channels
 - Display support:
   - v2/v3: Connectors for two different (Adafruit) OLED displays, or...
   - Nextion: A dedicated serial header
 - Local conotrol:
   - v2/v3: An encoder with a button
   - Nextion: these are touchscreens!
 - Support (footprints) for up to eight different sensors (you don't need them all!):
   - BME280
   - BME680 (Nextion versions only)
   - SHTC3
   - TMP117
   - DHT22
   - Up to two thermistors (internal/external)
   - SGP40 (WROVER/v3 and Nextion versions only)
 - The ability to draw power from one of three available AC circuits (RH/C, RC/C, or RMISC/C) or from an on-board barrel jack that supports both AC and DC
 - Ports that break out all I/O capability, including serial, I2C, SPI, encoder (v2/v3), and the on-board I/O expander

As a home automation enthusiast, I'm already using [Home Assistant](https://www.home-assistant.io) and as an electronics hobbyist, I was already using [ESPHome](https://esphome.io); it seemed a logical solution for this device and, as such, I designed it with [ESPHome](https://esphome.io) in mind. Still, I expect it will work just fine with any code that will run on the ESP32.

## The Journey

There aren't many hardware projects I do that do _not_ involve me writing at least some software -- this one was no exception. Prior to this, I was a more casual [ESPHome](https://esphome.io) user; I'd set up a device to control some LED lights in my 3-D printer's enclosure as well as another device as an IR blaster (see the [kbxIRBlaster](https://github.com/kbx81/kbxIRBlaster)) for my home AV system. This idea came to me and I began experimenting with some hardware on a breadboard. It was easy to get going, although I realized that some of the existing [ESPHome](https://esphome.io) components would need some tweaking to really get it to work to my liking.

Long story short, this led to me submitting a number of PRs to the [ESPHome](https://esphome.io) project. This is the first open source project I've contributed to! (Although I'm no stranger to GitHub -- I regularly use it at my day job.) With the help of several kind folks on the [ESPHome](https://esphome.io) Discord server, my PRs eventually got merged into their `dev` branch and are now generally available! I more or less rewrote the `bang-bang` component, although, after some discussion, we decided to make this a new component, which is cleverly named `thermostat`. I added support for two new displays and, as a part of one of them, also played a large part in adding color (and grayscale) support to the platform. With these changes, I was able to create a wonderful little device that should keep my place (and yours!) comfy for a long time to come.

## The Aftermath

Of course, just designing and building a controller such as this isn't enough. After you finish it, you have to do something with it. Why not _actually use it_? That's what it's for, right? ...Right?

That was kind of the whole point of this -- to make something better to replace what I had. And, as it turns out, it is a great solution. For one, temperature data is much higher resolution, both in terms of reported temperature and time. While not terribly useful, a resolution of (about) one-tenth of a degree F makes charts much more interesting, as you can see how (small) actions (turning on the TV and a couple lamps, or taking a shower, for example) quickly begin to affect the temperature and humidity.

I set up three of them -- one physically connected (with wires!) to the HVAC system and two satellite units (more on this [here](HARDWARE.md)). One satellite resides in the bedroom while the other is in the living room. I built automations that keep them all in sync so that a change on one of them is reflected on all of them (since it's really just a single heating system). The sensor data is averaged among them and the average is used to control the system. It is a great setup and it works beautifully!

## The Technical Stuff

Please see the [build guide](HARDWARE.md) for specific detail regarding the hardware and how to build one!

## Closing Thoughts

At the time I'm writing this, I've been using these devices for over a year and have found them to be very reliable -- significantly more so than what I was using before. The sensors are very accurate and provide a high-resolution picture of the climate/environment. They offer a lot of flexibility and can be built-to-order. They are very hackable and anyone familiar with ESP devices should be able to pick one up and run with it. You can extend them by plugging extra hardware into the break-outs along the edges of the boards. I really hope others will find them useful and have fun with them!

Some folks may be concerned about reliability. In my experience, this is simply not an issue, both with respect to this device itself as well as Home Assistant and ESPHome. Home Assistant and ESPHome are quite stable at this point and, if that isn't your experience, I might suggest looking more closely at your hardware setup and/or how you are managing it. A little troubleshooting and/or optimizing can go a long way. I've been using these platforms for over two years at this point (in two houses!) and I have had zero unexpected crashes. Now, _I have broken it_, but it has always been because of something I did and, as such, I was fully aware of it and easily recovered. Occasionally I'll stumble across an update that brings about a breaking change -- so I search the release notes for anything related to the device(s) that broke, I adjust my config as needed and move on. Breaking changes are an opportunity to learn and improve. I've got over a hundred connected devices and a plethora of automations at each location so _it all gets used_. When the software is set up correctly and the hardware is built well, it should be as reliable as the old mechanical light switch you used to use before you installed that smart one. ;)

Thank you for sticking around!

## Legal stuff and License

Everything you see here is provided to you free of charge. You are free to use it however you please within the constraints of the license -- but you do so at your own risk. I accept absolutely no liability if you cause damage to your property, HVAC system, or any other hardware you choose to connect to this device.

The circuit schematics, PCBs and enclosures found here are licensed under the
 [Creative Commons Attribution-ShareAlike 4.0 International License](http://creativecommons.org/licenses/by-sa/4.0/).



_Happy building!_

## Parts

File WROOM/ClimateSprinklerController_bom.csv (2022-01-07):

Component | Quantity Per PCB | References | Value | MPN1 | MPN2 | Footprint | Population
1 | 8 | C24 C25 C26 C27 C28 C29 C30 C31 | .01 uF | CC0805KRX7R9BB103 |  | C_0805_2012Metric
2 | 11 | C2 C4 C10 C11 C17 C18 C19 C20 C21 C22 C23 | 100 nF | CC0805KRX7R7BB104 |  | C_0805_2012Metric
3 | 1 | C7 | 220 nF | C2012X5R1H224K125AA |  | C_0805_2012Metric
4 | 1 | C8 | 1 uF | C0805C105K4RACTU |  | C_0805_2012Metric
5 | 2 | C5 C6 | 4.7 uF | C2012X5R1H475K125AB |  | C_0805_2012Metric
6 | 1 | C1 | 10 uF | C2012X5R1V106K085AC |  | C_0805_2012Metric
7 | 2 | C9 C12 | 10 uF | EEE-HP0J100R |  | CP_Elec_5x5.8
8 | 3 | C14 C15 C16 | 47 uF | GRM32ER61C476KE15L |  | C_1210_3225Metric
9 | 1 | C13 | 220 uF | EEE-HB0J221AP |  | CP_Elec_8x10
10 | 1 | C3 | 470 uF | EEV-FK1H471M |  | CP_Elec_16x17.5
11 | 1 | D1 | N/A | CD-MBL206SL |  | Diode_Bridge_Bourns_CD-MBL2xxS
12 | 3 | D5 D7 D9 | N/A | 1N4148W |  | D_SOD-123
13 | 1 | F1 | 300 mA | 2920L030DR |  | Fuse_2920_7451Metric
14 | 1 | J1 | 7.5 TO 40 V | 694106301002 |  | BarrelJack_Horizontal
15 | 2 | J11 J12 | HVAC | 1862039 |  | PhoenixContact_SPTAF_1_12-3.5-IL_1x12_P3.50mm_Vertical
16 | 3 | K1 K2 K3 | G5Q-1-DC5 | G5Q-1-DC5 |  | Relay_SPDT_Omron-G5Q-1
17 | 1 | L1 | 15 uH | 7447709150 | MSS1210-153MEB | L_Wuerth_WE-PD-Typ-LS
18 | 8 | Q6 Q7 Q8 Q9 Q10 Q11 Q12 Q13 | 2N6073B | 2N6073BG |  | TO-225-3_Vertical
19 | 4 | Q2 Q3 Q4 Q5 | 2N7002 | 2N7002 |  | SOT-23
20 | 1 | Q1 | TEPT5700 | TEPT5700 |  | LED_D5.0mm_Clear
21 | 8 | R55 R56 R57 R58 R59 R60 R61 R62 | 39 | ERJ-P06J390V |  | R_0805_2012Metric_Pad1.15x1.40mm_HandSolder
22 | 1 | R15 | 120 | RT0805FRE07120RL |  | R_0805_2012Metric_Pad1.15x1.40mm_HandSolder
23 | 8 | R39 R40 R41 R42 R43 R44 R45 R46 | 180 | RT0805FRE07180RL |  | R_0805_2012Metric_Pad1.15x1.40mm_HandSolder
24 | 8 | R31 R32 R33 R34 R35 R36 R37 R38 | 270 | RT0805FRE07270RL |  | R_0805_2012Metric_Pad1.15x1.40mm_HandSolder
25 | 3 | R20 R21 R22 | 560 | RT0805FRE07560RL |  | R_0805_2012Metric_Pad1.15x1.40mm_HandSolder
26 | 8 | R47 R48 R49 R50 R51 R52 R53 R54 | 820 | RT0805FRE07820RL |  | R_0805_2012Metric_Pad1.15x1.40mm_HandSolder
27 | 5 | R24 R25 R28 R29 R30 | 1K5 | RT0805FRE071K5L |  | R_0805_2012Metric_Pad1.15x1.40mm_HandSolder
28 | 1 | R12 | 1K6 | RT0805FRE071K6L |  | R_0805_2012Metric_Pad1.15x1.40mm_HandSolder
29 | 2 | R26 R27 | 2K7 | RT0805FRE072K7L |  | R_0805_2012Metric_Pad1.15x1.40mm_HandSolder
30 | 2 | R7 R8 | 3K3 | RT0805FRE073K3L |  | R_0805_2012Metric_Pad1.15x1.40mm_HandSolder
31 | 1 | R14 | 5K | CRCW08055K00JNTA |  | R_0805_2012Metric_Pad1.15x1.40mm_HandSolder
32 | 1 | R16 | 8K2 | RT0805FRE078K2L |  | R_0805_2012Metric_Pad1.15x1.40mm_HandSolder
33 | 11 | R1 R2 R3 R4 R5 R6 R13 R17 R18 R19 R23 | 10K | RC0805FR-0710KL |  | R_0805_2012Metric_Pad1.15x1.40mm_HandSolder
34 | 1 | R11 | 24.9K | RT0805FRE0724K9L |  | R_0805_2012Metric_Pad1.15x1.40mm_HandSolder
35 | 2 | R9 R10 | 100K | RC0805FR-07100KL |  | R_0805_2012Metric_Pad1.15x1.40mm_HandSolder
36 | 1 | RV1 | N/A | B72205S0400K101 |  | RV_Disc_D7mm_W4mm_P5mm
37 | 1 | SW2 | MODE | PTS645VK582LFS |  | SW_Tactile_SPST_Angled_PTS645Vx58-2LFS
38 | 1 | SW3 | PEC11S-929K-S0015 | PEC11S-929K-S0015 |  | RotaryEncoder_Bourns_PEC11S-Switch_Vertical_H9.5mm
39 | 1 | SW1 | RESET | PTS645VK582LFS |  | SW_Tactile_SPST_Angled_PTS645Vx58-2LFS
40 | 1 | TH1 | 10K | NXFT15XH103FA2B100 |  | PinSocket_1x02_P2.54mm_Vertical
41 | 1 | U7 | BME280 | BME280 |  | Bosch_LGA-8_2.5x2.5mm_P0.65mm_ClockwisePinNumbering
42 | 1 | U6 | DHT22 | DHT22 |  | PinSocket_1x04_P2.54mm_Vertical
43 | 1 | U1 | ESP32-WROOM-32D | ESP32-WROOM-32D |  | ESP32-WROOM-32
44 | 1 | U4 | LD1086DT33TR | LD1086DT33TR |  | TO-252-2
45 | 1 | U3 | LMR36520 | LMR36520ADDAR |  | Texas_HSOP-8-1EP_3.9x4.9mm_P1.27mm_ThermalVias
46 | 1 | U2 | MCP23017_SO | MCP23017-E/SO |  | SOIC-28W_7.5x17.9mm_P1.27mm
47 | 8 | U9 U10 U11 U12 U13 U14 U15 U16 | MOC3043 | MOC3043SM |  | SMDIP-6_W9.53mm
48 | 1 | U8 | SHTC3 | SHTC3 |  | AMS_QFN-4-1EP_2x2mm_P0.95mm_EP0.7x1.6mm
49 | 1 | U5 | TMP117 | TMP117MAIDRVR |  | WSON-6-1EP_2x2mm_P0.65mm_EP1x1.6mm
Component Groups: | 64
Component Count: | 158
Fitted Components: | 139
Number of PCBs: | 1
Total components: | 139
Schematic Version: | 2
Schematic Date: | 2020-08-14
PCB Variant: | udefault
BoM Date: | Thursday, March 25, 2021 at 01:13:09 AM
Schematic Source: | ClimateSprinklerController.sch
KiCad Version: | Eeschema (5.1.9-0-10_14)

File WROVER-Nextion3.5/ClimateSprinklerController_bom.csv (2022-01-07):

Component | Quantity Per PCB | References | Value | MPN1 | MPN2 | Footprint | Population
1 | 16 | C2 C4 C10 C11 C15 C17 C19 C23 C24 C25 C26 C27 C28 C29 C30 C31 | 100 nF | CC0805KRX7R7BB104 |  | C_0805_2012Metric
2 | 1 | C8 | 220 nF | C2012X5R1H224K125AA |  | C_0805_2012Metric
3 | 3 | C9 C20 C21 | 1 uF | C0805C105K4RACTU |  | C_0805_2012Metric
4 | 4 | C1 C6 C7 C13 | 4.7 uF | C2012X5R1H475K125AB |  | C_0805_2012Metric
5 | 2 | C18 C22 | 10 uF | EEE-HP0J100R |  | CP_Elec_5x5.8
6 | 1 | C3 | 10 uF | C2012X5R1V106K085AC |  | C_0805_2012Metric
7 | 3 | C12 C14 C16 | 47 uF | GRM32ER61C476KE15L |  | C_1210_3225Metric
8 | 1 | C5 | 100 µF | 25SVF100M |  | CP_Elec_8x10
9 | 2 | D1 D2 | N/A | MBR230S1F-7 |  | D_SOD-123F
10 | 1 | F1 | 750 mA | 2920L075 |  | Fuse_2920_7451Metric
11 | 1 | J2 | 5 TO 40 V* | 694106301002 |  | BarrelJack_Horizontal
12 | 1 | J1 | N/A | 105017-0001 |  | USB_Micro-B_Molex-105017-0001
13 | 1 | L1 | 15 uH | 7447709150 | MSS1210-153MEB | L_Wuerth_WE-PD-Typ-LS
14 | 2 | Q1 Q2 | MMSS8050 | MMSS8050 |  | SOT-23
15 | 1 | Q3 | TEPT5700 | TEPT5700 |  | LED_D5.0mm_Clear
16 | 2 | R17 R18 | 4.7 | RC0805FR-074R7L |  | R_0805_2012Metric_Pad1.20x1.40mm_HandSolder
17 | 1 | R21 | 120 | RT0805FRE07120RL |  | R_0805_2012Metric_Pad1.20x1.40mm_HandSolder
18 | 1 | R3 | 1K2 | RT0805FRE072K7L |  | R_0805_2012Metric_Pad1.20x1.40mm_HandSolder
19 | 1 | R19 | 1K6 | RT0805FRE071K6L |  | R_0805_2012Metric_Pad1.20x1.40mm_HandSolder
20 | 1 | R4 | 2K7 | RT0805FRE072K7L |  | R_0805_2012Metric_Pad1.20x1.40mm_HandSolder
21 | 2 | R6 R8 | 3K3 | RT0805FRE073K3L |  | R_0805_2012Metric_Pad1.20x1.40mm_HandSolder
22 | 1 | R1 | 4K7 | RT0805FRE074K7L |  | R_0805_2012Metric_Pad1.20x1.40mm_HandSolder
23 | 1 | R23 | 5K | CRCW08055K00JNTA |  | R_0805_2012Metric_Pad1.20x1.40mm_HandSolder
24 | 1 | R16 | 8K2 | RT0805FRE078K2L |  | R_0805_2012Metric_Pad1.20x1.40mm_HandSolder
25 | 12 | R2 R5 R7 R11 R12 R13 R14 R15 R22 R24 R25 R26 | 10K | RC0805FR-0710KL |  | R_0805_2012Metric_Pad1.20x1.40mm_HandSolder
26 | 1 | R10 | 24.9K | RT0805FRE0724K9L |  | R_0805_2012Metric_Pad1.20x1.40mm_HandSolder
27 | 2 | R9 R20 | 100K | RC0805FR-07100KL |  | R_0805_2012Metric_Pad1.20x1.40mm_HandSolder
28 | 1 | SW3 | MODE | PTS645VK582LFS |  | SW_Tactile_SPST_Angled_PTS645Vx58-2LFS
29 | 1 | SW1 | POWER | 48BFSP1M6QT |  | SW_Push_1P2T_Vertical_E-Switch_800UDP8P1A1M6
30 | 1 | SW2 | RESET | PTS645VK582LFS |  | SW_Tactile_SPST_Angled_PTS645Vx58-2LFS
31 | 2 | TH1 TH2 | 10K | NXFT15XH103FA2B100 |  | PinSocket_1x02_P2.54mm_Vertical
32 | 1 | U10 | BME280 | BME280 |  | Bosch_LGA-8_2.5x2.5mm_P0.65mm_ClockwisePinNumbering
33 | 1 | U8 | BME680 | BME680 |  | Bosch_LGA-8_3x3mm_P0.8mm_ClockwisePinNumbering
34 | 1 | U11 | DHT22 | DHT22 |  | PinSocket_1x04_P2.54mm_Vertical
35 | 1 | U1 | ESP32-WROVER | ESP32-WROVER |  | ESP32-WROVER
36 | 1 | U2 | FT232RL | FT232RL |  | SSOP-28_5.3x10.2mm_P0.65mm
37 | 1 | U6 | LD1086DT33TR | LD1086DT33TR |  | TO-252-2
38 | 1 | U3 | LMR36520 | LMR36520ADDAR |  | Texas_HSOP-8-1EP_3.9x4.9mm_P1.27mm_ThermalVias
39 | 1 | U5 | SGP40 | SGP40 |  | DFN-6-1EP_2.44x2.44mm_P0.8mm_EP1.25x1.7mm
40 | 1 | U7 | SHTC3 | SHTC3 |  | AMS_QFN-4-1EP_2x2mm_P0.95mm_EP0.7x1.6mm
41 | 1 | U9 | TMP117 | TMP117MAIDRVR |  | WSON-6-1EP_2x2mm_P0.65mm_EP1x1.6mm
42 | 1 | U4 | TPS22917DBV | TPS22917DBV |  | SOT-23-6
Component Groups: | 53
Component Count: | 96
Fitted Components: | 82
Number of PCBs: | 1
Total components: | 82
Schematic Version: | 2
Schematic Date: | 2020-08-14
PCB Variant: | udefault
BoM Date: | Thursday, March 25, 2021 at 12:49:10 AM
Schematic Source: | ClimateSprinklerController.sch
KiCad Version: | Eeschema (5.1.9-0-10_14)

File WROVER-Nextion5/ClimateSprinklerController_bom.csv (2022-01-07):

Component | Quantity Per PCB | References | Value | MPN1 | MPN2 | Footprint | Population
1 | 5 | C33 C34 C35 C36 C37 | .01 uF | CC0805KRX7R9BB103 |  | C_0805_2012Metric
2 | 17 | C3 C4 C6 C8 C10 C11 C15 C17 C22 C23 C24 C26 C28 C29 C30 C31 C32 | 100 nF | CC0805KRX7R7BB104 |  | C_0805_2012Metric
3 | 1 | C13 | 220 nF | C2012X5R1H224K125AA |  | C_0805_2012Metric
4 | 3 | C14 C19 C20 | 1 uF | C0805C105K4RACTU |  | C_0805_2012Metric
5 | 4 | C2 C5 C9 C12 | 4.7 uF | C2012X5R1H475K125AB |  | C_0805_2012Metric
6 | 1 | C1 | 10 uF | C2012X5R1V106K085AC |  | C_0805_2012Metric
7 | 2 | C25 C27 | 10 uF | EEE-HP0J100R |  | CP_Elec_5x5.8
8 | 3 | C16 C18 C21 | 47 uF | GRM32ER61C476KE15L |  | C_1210_3225Metric
9 | 1 | C7 | 470 uF | UVK1H471MPD |  | CP_Radial_Cutout_L20.0mm_D10.0mm_P5.00mm
10 | 1 | D1 | N/A | MBR230S1F-7 |  | D_SOD-123F
11 | 1 | D2 | N/A | CD-MBL206SL |  | Diode_Bridge_Bourns_CD-MBL2xxS
12 | 1 | D9 | N/A | 1N4148W |  | D_SOD-123
13 | 1 | F1 | 300 mA | 2920L030DR |  | Fuse_2920_7451Metric
14 | 1 | J1 | 7.5 TO 40 V | 694106301002 |  | BarrelJack_Horizontal
15 | 1 | J10 | HVAC | 1862039 |  | PhoenixContact_SPTAF_1_12-3.5-IL_1x12_P3.50mm_Vertical
16 | 1 | J2 | N/A | 105017-0001 |  | USB_Micro-B_Molex-105017-0001
17 | 1 | K1 | G6E-134P-US DC5 | G6E-134P-US DC5 |  | Relay_SPDT_Omron_G6E
18 | 1 | L1 | 15 uH | 7447709150 | MSS1210-153MEB | L_Wuerth_WE-PD-Typ-LS
19 | 5 | Q5 Q6 Q7 Q8 Q9 | 2N6073BG | 2N6073BG |  | TO-225-3_Vertical
20 | 1 | Q4 | 2N7002 | 2N7002 |  | SOT-23
21 | 2 | Q1 Q2 | MMSS8050 | MMSS8050 |  | SOT-23
22 | 1 | Q3 | TEPT5700 | TEPT5700 |  | LED_D5.0mm_Clear
23 | 2 | R12 R20 | 4.7 | RC0805FR-074R7L |  | R_0805_2012Metric_Pad1.20x1.40mm_HandSolder
24 | 5 | R51 R52 R53 R54 R55 | 39 | ERJ-P06J390V |  | R_0805_2012Metric_Pad1.20x1.40mm_HandSolder
25 | 1 | R28 | 120 | RT0805FRE07120RL |  | R_0805_2012Metric_Pad1.20x1.40mm_HandSolder
26 | 5 | R40 R41 R42 R43 R44 | 180 | RT0805FRE07180RL |  | R_0805_2012Metric_Pad1.20x1.40mm_HandSolder
27 | 5 | R35 R36 R37 R38 R39 | 270 | RT0805FRE07270RL |  | R_0805_2012Metric_Pad1.20x1.40mm_HandSolder
28 | 1 | R29 | 560 | RT0805FRE07560RL |  | R_0805_2012Metric_Pad1.20x1.40mm_HandSolder
29 | 5 | R45 R46 R47 R48 R49 | 820 | RT0805FRE07820RL |  | R_0805_2012Metric_Pad1.20x1.40mm_HandSolder
30 | 1 | R9 | 1K2 | RT0805FRE072K7L |  | R_0805_2012Metric_Pad1.20x1.40mm_HandSolder
31 | 2 | R31 R32 | 1K5 | RT0805FRE071K5L |  | R_0805_2012Metric_Pad1.20x1.40mm_HandSolder
32 | 1 | R27 | 1K6 | RT0805FRE071K6L |  | R_0805_2012Metric_Pad1.20x1.40mm_HandSolder
33 | 3 | R10 R33 R34 | 2K7 | RT0805FRE072K7L |  | R_0805_2012Metric_Pad1.20x1.40mm_HandSolder
34 | 2 | R18 R21 | 3K3 | RT0805FRE073K3L |  | R_0805_2012Metric_Pad1.20x1.40mm_HandSolder
35 | 1 | R4 | 4K7 | RT0805FRE074K7L |  | R_0805_2012Metric_Pad1.20x1.40mm_HandSolder
36 | 1 | R23 | 5K | CRCW08055K00JNTA |  | R_0805_2012Metric_Pad1.20x1.40mm_HandSolder
37 | 1 | R24 | 8K2 | RT0805FRE078K2L |  | R_0805_2012Metric_Pad1.20x1.40mm_HandSolder
38 | 16 | R1 R2 R3 R5 R6 R7 R8 R11 R13 R14 R15 R22 R25 R26 R30 R50 | 10K | RC0805FR-0710KL |  | R_0805_2012Metric_Pad1.20x1.40mm_HandSolder
39 | 1 | R17 | 24.9K | RT0805FRE0724K9L |  | R_0805_2012Metric_Pad1.20x1.40mm_HandSolder
40 | 2 | R16 R19 | 100K | RC0805FR-07100KL |  | R_0805_2012Metric_Pad1.20x1.40mm_HandSolder
41 | 1 | RV1 | N/A | B72205S0400K101 |  | RV_Disc_D7mm_W4mm_P5mm
42 | 1 | SW3 | MODE | PTS645VK582LFS |  | SW_Tactile_SPST_Angled_PTS645Vx58-2LFS
43 | 1 | SW1 | POWER | 48BFSP1M6QT |  | SW_Push_1P2T_Vertical_E-Switch_800UDP8P1A1M6
44 | 1 | SW2 | RESET | PTS645VK582LFS |  | SW_Tactile_SPST_Angled_PTS645Vx58-2LFS
45 | 2 | TH1 TH2 | 10K | NXFT15XH103FA2B100 |  | PinSocket_1x02_P2.54mm_Vertical
46 | 1 | U9 | BME280 | BME280 |  | Bosch_LGA-8_2.5x2.5mm_P0.65mm_ClockwisePinNumbering
47 | 1 | U7 | BME680 | BME680 |  | Bosch_LGA-8_3x3mm_P0.8mm_ClockwisePinNumbering
48 | 1 | U17 | DHT22 | DHT22 |  | PinSocket_1x04_P2.54mm_Vertical
49 | 1 | U1 | ESP32-WROVER | ESP32-WROVER |  | ESP32-WROVER
50 | 1 | U3 | FT232RL | FT232RL |  | SSOP-28_5.3x10.2mm_P0.65mm
51 | 1 | U8 | LD1086DT33TR | LD1086DT33TR |  | TO-252-2
52 | 1 | U5 | LMR36520 | LMR36520ADDAR |  | Texas_HSOP-8-1EP_3.9x4.9mm_P1.27mm_ThermalVias
53 | 1 | U2 | MCP23017_SO | MCP23017-E/SO |  | SOIC-28W_7.5x17.9mm_P1.27mm
54 | 5 | U12 U13 U14 U15 U16 | MOC3043 | MOC3043SM |  | SMDIP-6_W9.53mm
55 | 1 | U6 | SGP40 | SGP40 |  | DFN-6-1EP_2.44x2.44mm_P0.8mm_EP1.25x1.7mm
56 | 1 | U10 | SHTC3 | SHTC3 |  | AMS_QFN-4-1EP_2x2mm_P0.95mm_EP0.7x1.6mm
57 | 1 | U11 | TMP117 | TMP117MAIDRVR |  | WSON-6-1EP_2x2mm_P0.65mm_EP1x1.6mm
58 | 1 | U4 | TPS22917DBV | TPS22917DBV |  | SOT-23-6
Component Groups: | 74
Component Count: | 151
Fitted Components: | 133
Number of PCBs: | 1
Total components: | 133
Schematic Version: | 2
Schematic Date: | 2020-08-14
PCB Variant: | udefault
BoM Date: | Thursday, March 25, 2021 at 12:44:02 AM
Schematic Source: | ClimateSprinklerController.sch
KiCad Version: | Eeschema (5.1.9-0-10_14)

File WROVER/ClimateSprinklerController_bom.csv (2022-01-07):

Component | Quantity Per PCB | References | Value | MPN1 | MPN2 | Footprint | Population
1 | 8 | C26 C27 C28 C29 C30 C31 C32 C33 | .01 uF | CC0805KRX7R9BB103 |  | C_0805_2012Metric
2 | 11 | C2 C4 C10 C11 C19 C20 C21 C22 C23 C24 C25 | 100 nF | CC0805KRX7R7BB104 |  | C_0805_2012Metric
3 | 1 | C7 | 220 nF | C2012X5R1H224K125AA |  | C_0805_2012Metric
4 | 3 | C8 C15 C16 | 1 uF | C0805C105K4RACTU |  | C_0805_2012Metric
5 | 2 | C5 C6 | 4.7 uF | C2012X5R1H475K125AB |  | C_0805_2012Metric
6 | 1 | C1 | 10 uF | C2012X5R1V106K085AC |  | C_0805_2012Metric
7 | 2 | C9 C12 | 10 uF | EEE-HP0J100R |  | CP_Elec_5x5.8
8 | 3 | C14 C17 C18 | 47 uF | GRM32ER61C476KE15L |  | C_1210_3225Metric
9 | 1 | C13 | 220 uF | EEE-HB0J221AP |  | CP_Elec_8x10
10 | 1 | C3 | 470 uF | EEV-FK1H471M |  | CP_Elec_16x17.5
11 | 1 | D1 | N/A | CD-MBL206SL |  | Diode_Bridge_Bourns_CD-MBL2xxS
12 | 3 | D5 D7 D9 | N/A | 1N4148W |  | D_SOD-123
13 | 1 | F1 | 300 mA | 2920L030DR |  | Fuse_2920_7451Metric
14 | 1 | J1 | 7.5 TO 40 V | 694106301002 |  | BarrelJack_Horizontal
15 | 2 | J11 J12 | HVAC | 1862039 |  | PhoenixContact_SPTAF_1_12-3.5-IL_1x12_P3.50mm_Vertical
16 | 3 | K1 K2 K3 | G5Q-1-DC5 | G5Q-1-DC5 |  | Relay_SPDT_Omron-G5Q-1
17 | 1 | L1 | 15 uH | 7447709150 | MSS1210-153MEB | L_Wuerth_WE-PD-Typ-LS
18 | 8 | Q5 Q6 Q7 Q8 Q9 Q10 Q11 Q12 | 2N6073B | 2N6073BG |  | TO-225-3_Vertical
19 | 3 | Q2 Q3 Q4 | 2N7002 | 2N7002 |  | SOT-23
20 | 1 | Q1 | TEPT5700 | TEPT5700 |  | LED_D5.0mm_Clear
21 | 1 | R12 | 4.7 | RC0805FR-07100KL |  | R_0805_2012Metric_Pad1.20x1.40mm_HandSolder
22 | 8 | R58 R59 R60 R61 R62 R63 R64 R65 | 39 | ERJ-P06J390V |  | R_0805_2012Metric_Pad1.20x1.40mm_HandSolder
23 | 1 | R18 | 120 | RT0805FRE07120RL |  | R_0805_2012Metric_Pad1.20x1.40mm_HandSolder
24 | 8 | R42 R43 R44 R45 R46 R47 R48 R49 | 180 | RT0805FRE07180RL |  | R_0805_2012Metric_Pad1.20x1.40mm_HandSolder
25 | 8 | R34 R35 R36 R37 R38 R39 R40 R41 | 270 | RT0805FRE07270RL |  | R_0805_2012Metric_Pad1.20x1.40mm_HandSolder
26 | 3 | R23 R24 R25 | 560 | RT0805FRE07560RL |  | R_0805_2012Metric_Pad1.20x1.40mm_HandSolder
27 | 8 | R50 R51 R52 R53 R54 R55 R56 R57 | 820 | RT0805FRE07820RL |  | R_0805_2012Metric_Pad1.20x1.40mm_HandSolder
28 | 5 | R27 R28 R31 R32 R33 | 1K5 | RT0805FRE071K5L |  | R_0805_2012Metric_Pad1.20x1.40mm_HandSolder
29 | 1 | R15 | 1K6 | RT0805FRE071K6L |  | R_0805_2012Metric_Pad1.20x1.40mm_HandSolder
30 | 2 | R29 R30 | 2K7 | RT0805FRE072K7L |  | R_0805_2012Metric_Pad1.20x1.40mm_HandSolder
31 | 2 | R9 R10 | 3K3 | RT0805FRE073K3L |  | R_0805_2012Metric_Pad1.20x1.40mm_HandSolder
32 | 1 | R17 | 5K | CRCW08055K00JNTA |  | R_0805_2012Metric_Pad1.20x1.40mm_HandSolder
33 | 1 | R19 | 8K2 | RT0805FRE078K2L |  | R_0805_2012Metric_Pad1.20x1.40mm_HandSolder
34 | 13 | R1 R2 R3 R4 R5 R6 R7 R8 R16 R20 R21 R22 R26 | 10K | RC0805FR-0710KL |  | R_0805_2012Metric_Pad1.20x1.40mm_HandSolder
35 | 1 | R14 | 24.9K | RT0805FRE0724K9L |  | R_0805_2012Metric_Pad1.20x1.40mm_HandSolder
36 | 2 | R11 R13 | 100K | RC0805FR-07100KL |  | R_0805_2012Metric_Pad1.20x1.40mm_HandSolder
37 | 1 | RV1 | N/A | B72205S0400K101 |  | RV_Disc_D7mm_W4mm_P5mm
38 | 1 | SW2 | MODE | PTS645VK582LFS |  | SW_Tactile_SPST_Angled_PTS645Vx58-2LFS
39 | 1 | SW3 | PEC11S-929K-S0015 | PEC11S-929K-S0015 |  | RotaryEncoder_Bourns_PEC11S-Switch_Vertical_H9.5mm
40 | 1 | SW1 | RESET | PTS645VK582LFS |  | SW_Tactile_SPST_Angled_PTS645Vx58-2LFS
41 | 1 | TH1 | 10K | NXFT15XH103FA2B100 |  | PinSocket_1x02_P2.54mm_Vertical
42 | 1 | U8 | BME280 | BME280 |  | Bosch_LGA-8_2.5x2.5mm_P0.65mm_ClockwisePinNumbering
43 | 1 | U7 | DHT22 | DHT22 |  | PinSocket_1x04_P2.54mm_Vertical
44 | 1 | U1 | ESP32-WROVER | ESP32-WROVER |  | ESP32-WROVER
45 | 1 | U4 | LD1086DT33TR | LD1086DT33TR |  | TO-252-2
46 | 1 | U3 | LMR36520 | LMR36520ADDAR |  | Texas_HSOP-8-1EP_3.9x4.9mm_P1.27mm_ThermalVias
47 | 1 | U2 | MCP23017_SO | MCP23017-E/SO |  | SOIC-28W_7.5x17.9mm_P1.27mm
48 | 8 | U10 U11 U12 U13 U14 U15 U16 U17 | MOC3043 | MOC3043SM |  | SMDIP-6_W9.53mm
49 | 1 | U5 | SGP40 | SGP40 |  | DFN-6-1EP_2.44x2.44mm_P0.8mm_EP1.25x1.7mm
50 | 1 | U9 | SHTC3 | SHTC3 |  | AMS_QFN-4-1EP_2x2mm_P0.95mm_EP0.7x1.6mm
51 | 1 | U6 | TMP117 | TMP117MAIDRVR |  | WSON-6-1EP_2x2mm_P0.65mm_EP1x1.6mm
Component Groups: | 67
Component Count: | 164
Fitted Components: | 144
Number of PCBs: | 1
Total components: | 144
Schematic Version: | 2
Schematic Date: | 2020-08-14
PCB Variant: | udefault
BoM Date: | Thursday, March 25, 2021 at 01:11:38 AM
Schematic Source: | ClimateSprinklerController.sch
KiCad Version: | Eeschema (5.1.9-0-10_14)

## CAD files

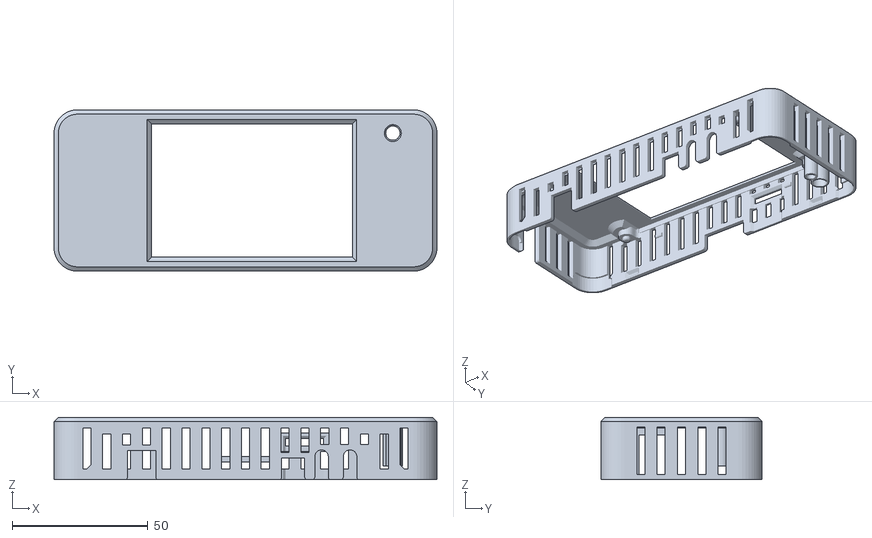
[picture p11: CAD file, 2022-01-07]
enclosures/Nextion3.5/TopCover.stl
141.0 x 59.4 x 23.0

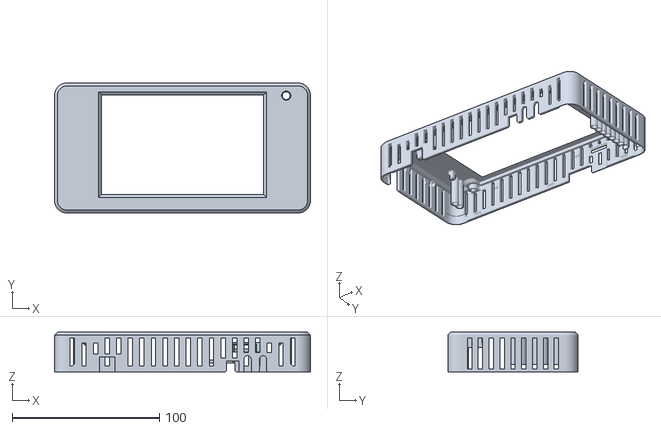
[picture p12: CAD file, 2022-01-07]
enclosures/Nextion5-Pseries/TopCover.stl
174.0 x 88.5 x 27.0

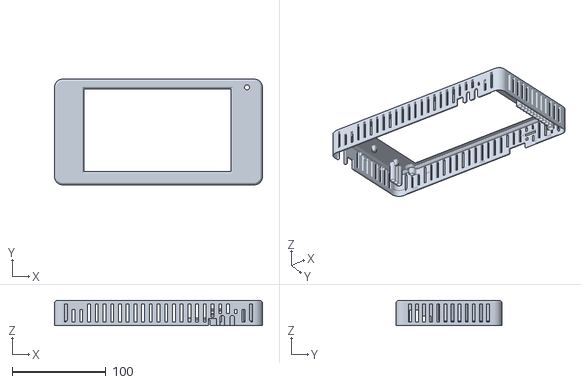
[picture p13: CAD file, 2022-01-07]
enclosures/Nextion7/TopCover.stl
221.5 x 112.5 x 27.0

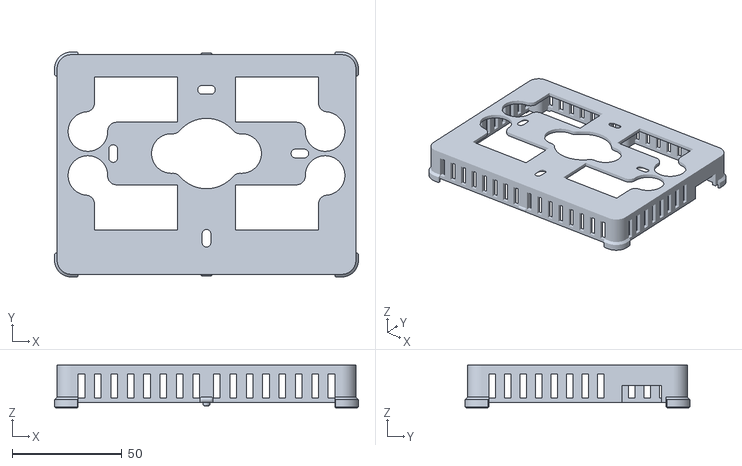
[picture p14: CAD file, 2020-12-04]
enclosures/OLED128x64/no_power_jack/EnclosureBottom.stl
138.4 x 102.4 x 19.4

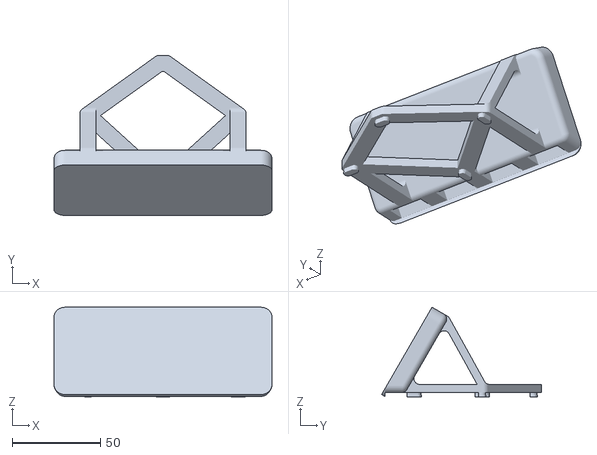
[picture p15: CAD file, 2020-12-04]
enclosures/OLED128x64/Stand.stl
123.2 x 90.4 x 50.6

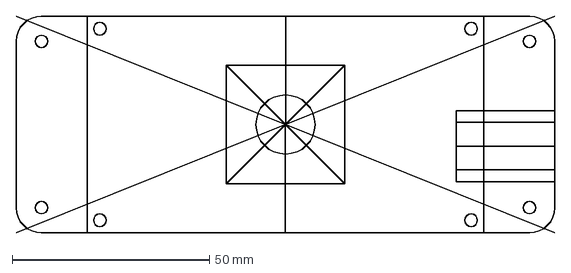
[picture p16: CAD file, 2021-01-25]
WROVER-Nextion3.5/ClimateSprinklerController.dxf
136.5 x 54.9 mm

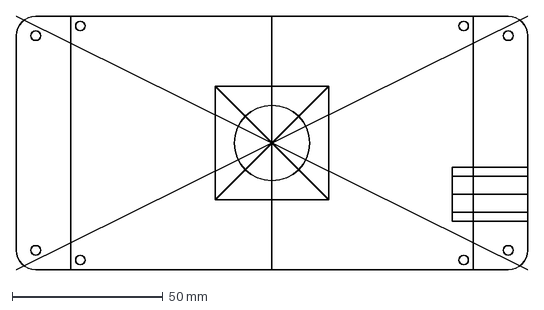
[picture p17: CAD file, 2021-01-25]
WROVER-Nextion5/ClimateSprinklerController.dxf
169.5 x 84.0 mm

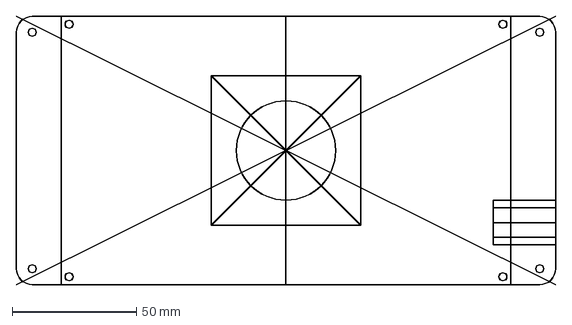
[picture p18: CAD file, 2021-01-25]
WROVER-Nextion7/ClimateSprinklerController.dxf
217.0 x 108.0 mm

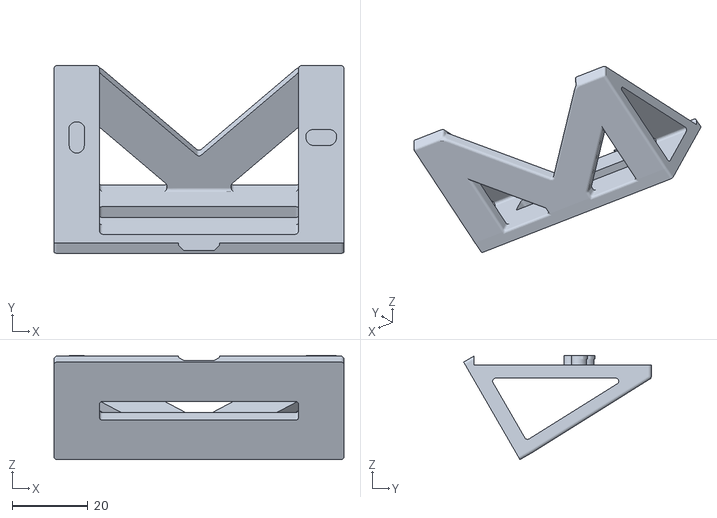
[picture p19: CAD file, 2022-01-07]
enclosures/Nextion3.5/Stand.stl
76.5 x 49.5 x 27.5

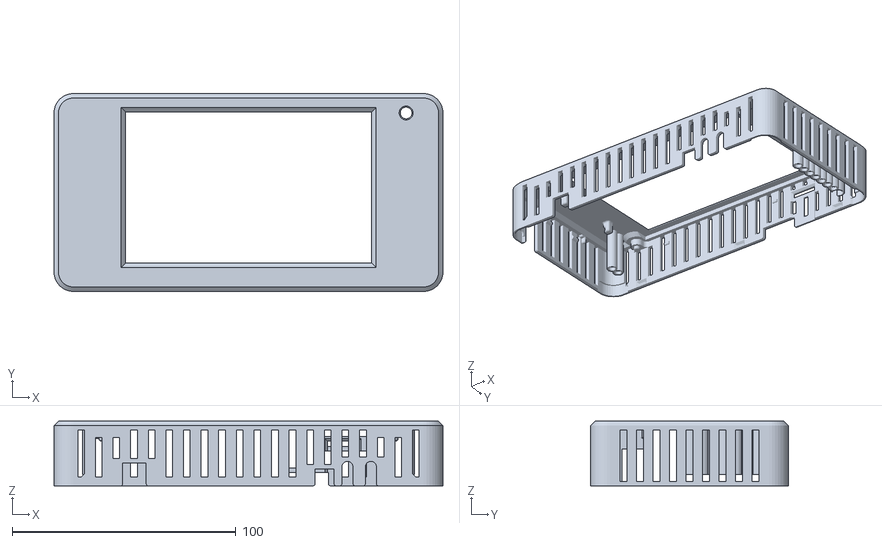
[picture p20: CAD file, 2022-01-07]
enclosures/Nextion5-Pseries/TopCover-deep.stl
174.0 x 88.5 x 29.0

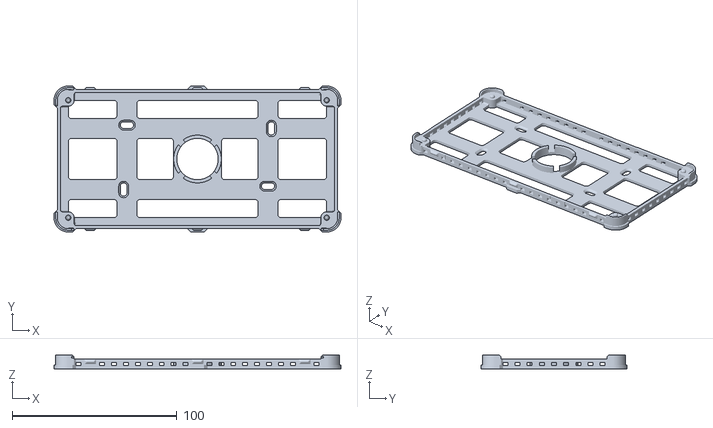
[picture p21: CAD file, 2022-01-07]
enclosures/Nextion5/BackCover.stl
174.0 x 88.5 x 8.60

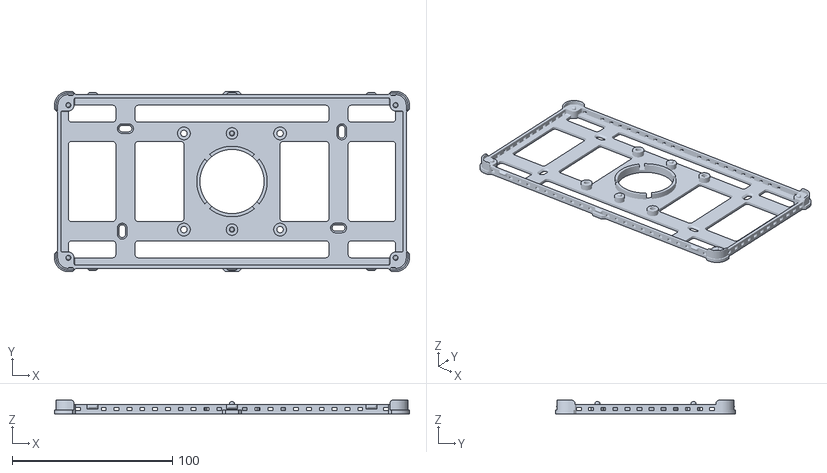
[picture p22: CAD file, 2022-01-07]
enclosures/Nextion7/BackCover.stl
221.5 x 112.5 x 8.60

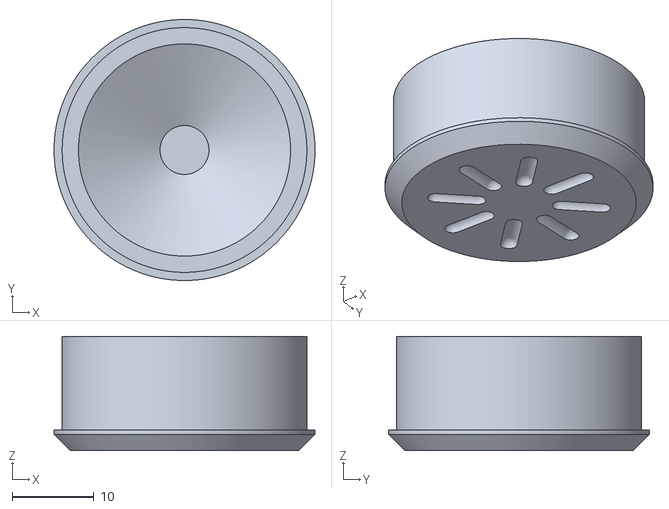
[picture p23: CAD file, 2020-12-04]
enclosures/OLED128x64/Knob.stl
32.0 x 32.0 x 14.0

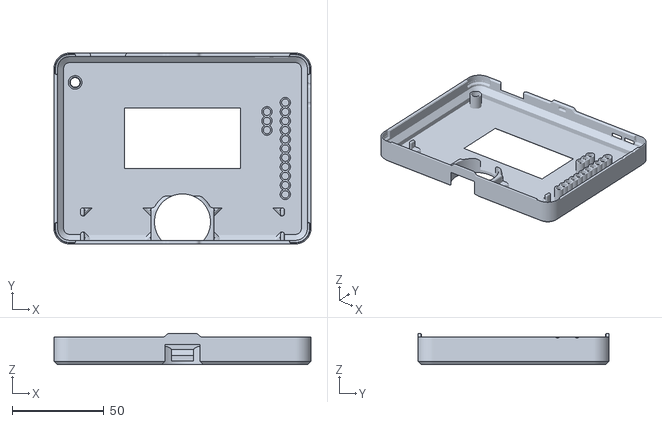
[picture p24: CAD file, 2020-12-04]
enclosures/OLED128x64/no_power_jack/EnclosureTopCover.stl
140.0 x 104.0 x 17.0

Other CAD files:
enclosures/Nextion5/TopCover-NoJack-NoSwitch.stl
enclosures/OLED128x64/power_jack/EnclosureBottom.stl
enclosures/OLED128x64/power_jack/EnclosureTopCover.stl
enclosures/Nextion3.5/BackCover.stl
enclosures/Nextion5-Pseries/BackCover.stl
enclosures/Nextion5-Pseries/Stand.stl
enclosures/Nextion5-Pseries/TopCover-NoJack-NoSwitch.stl
enclosures/Nextion5/Stand.stl
enclosures/Nextion5/TopCover.stl
enclosures/Nextion7/Stand.stl
enclosures/Nextion7/TopCover-NoJack-NoSwitch.stl

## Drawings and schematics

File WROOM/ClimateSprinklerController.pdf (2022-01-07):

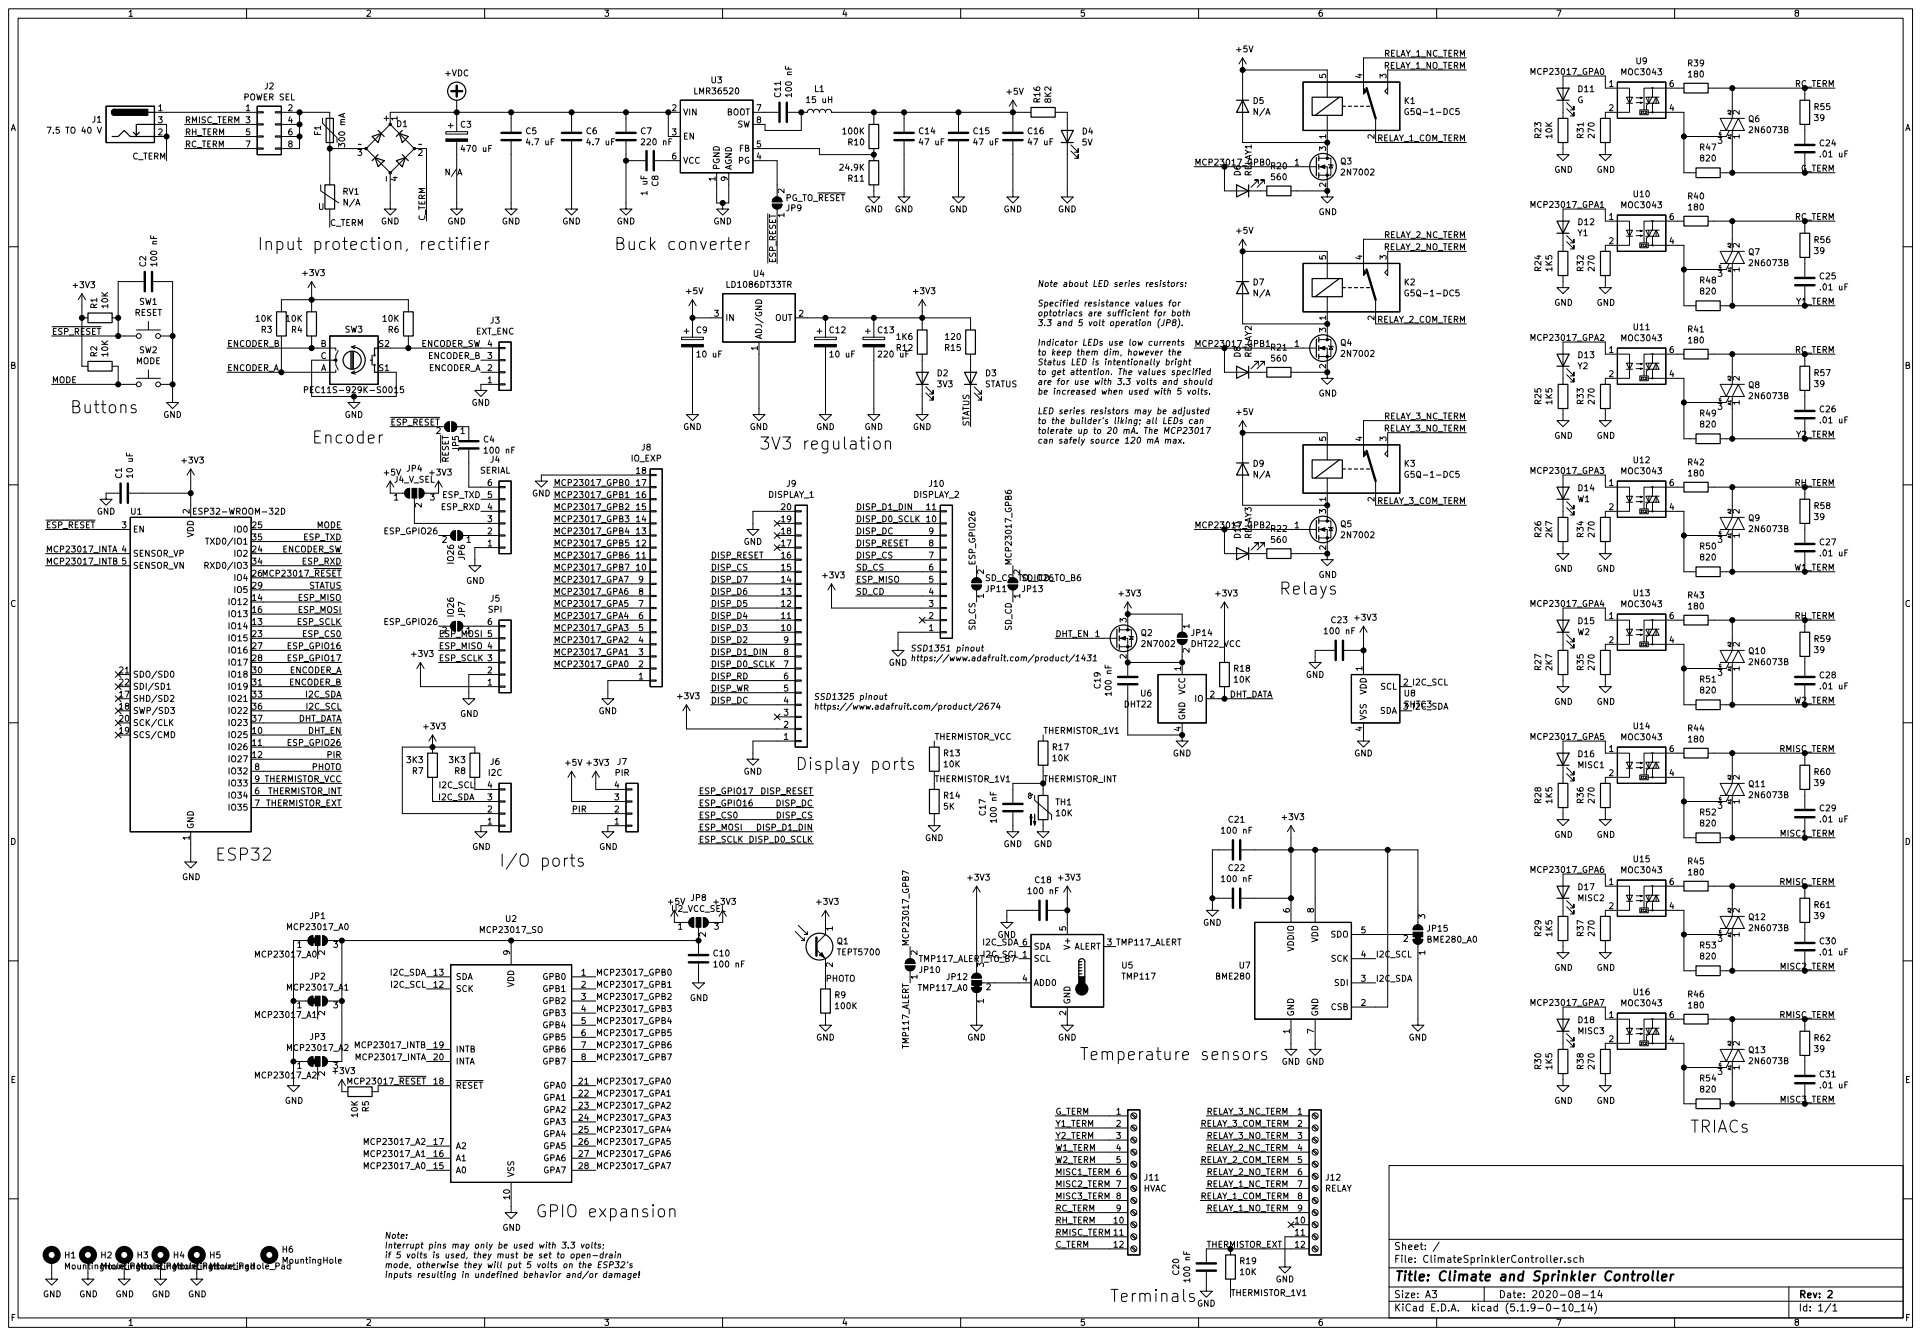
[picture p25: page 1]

1 VIN 2 EN 3 PG 4 FB 5 VCC 6 BOOT 7 SW 8 AGND

Note about LED series resistors: Specified resistance values for

optotriacs are sufficient for both
3.3 and 5 volt operation (JP8).
6 U11 MOC3043 C18 +3V3
Indicator LEDs use low currents
to keep them dim, however the
Status LED is intentionally bright
to get attention. The values specified
are for use with 3.3 volts and should
be increased when used with 5 volts. LED series resistors may be adjusted

to the builders liking; all LEDs can
820 GND
tolerate up to 20 mA. The MCP23017
can safely source 120 mA max.

2 SCK/CLK 20 SDO/SD0 21 SDI/SD1 22

GND GND GND GND GND

SSD1351 pinout
https://www.adafruit.com/product/1431

1 CSB 2 SDI 3 SCK 4 SDO 5 VDDIO

Note:
Interrupt pins may only be used with 3.3 volts;
if 5 volts is used, they must be set to open-drain
mode, otherwise they will put 5 volts on the ESP32s
inputs resulting in undefined behavior and/or damage!

File: ClimateSprinklerController.sch Sheet: /
Id: 1/1 Title: Climate and Sprinkler Controller

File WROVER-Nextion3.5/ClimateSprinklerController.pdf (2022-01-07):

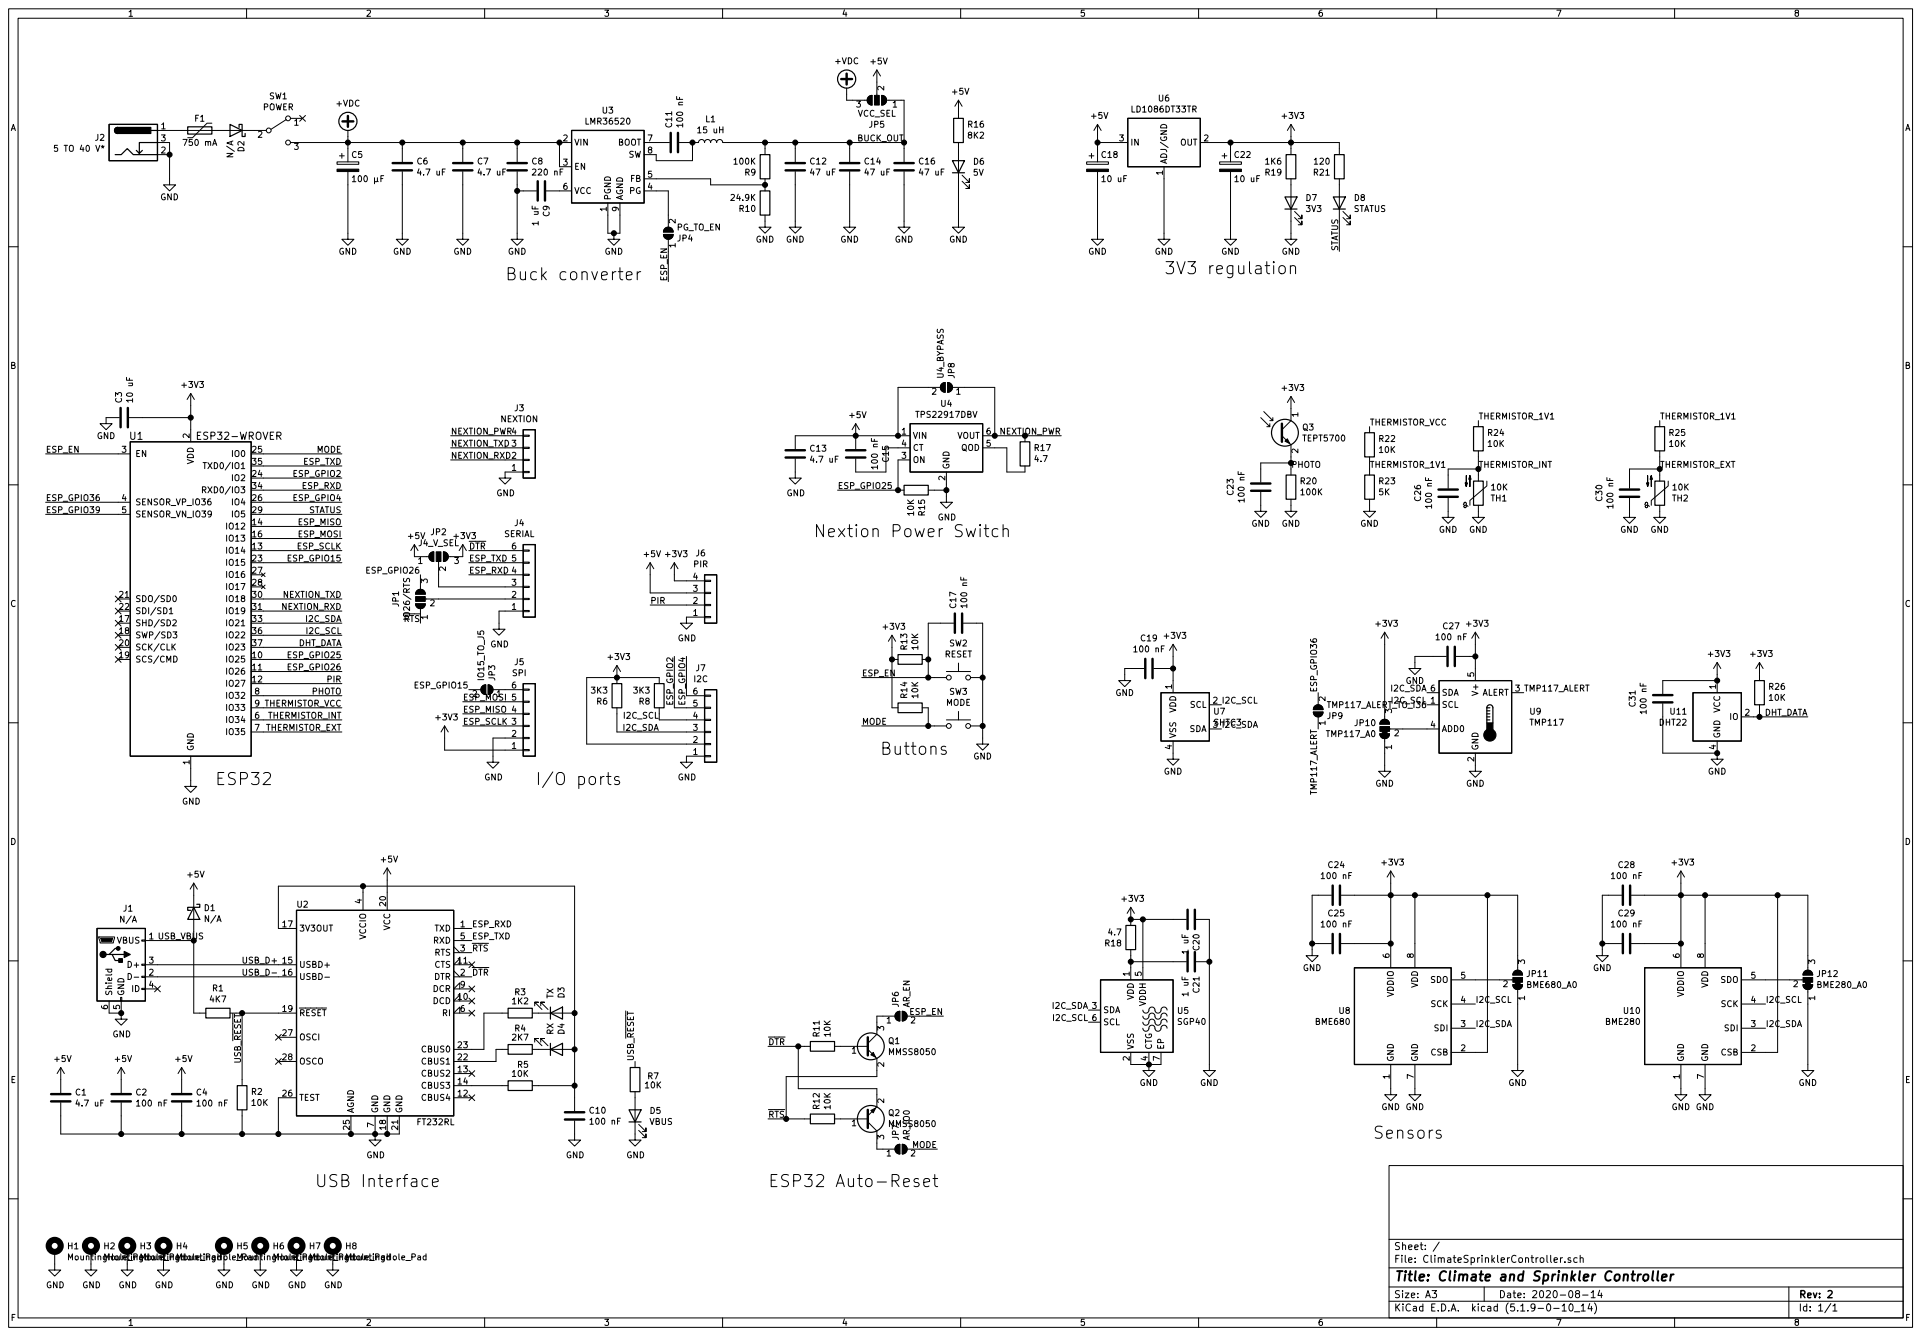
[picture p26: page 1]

1 VIN 2 EN 3 PG 4 FB 5 VCC 6 BOOT 7 SW 8 AGND

2 ON 3 CT 4 QOD 5 VOUT 6 U4 TPS22917DBV R8

2 SCK/CLK 20 SDO/SD0 21 SDI/SD1 22

File: ClimateSprinklerController.sch Sheet: / GND

1 CSB 2 SDI 3 SCK 4 SDO 5 VDDIO

Id: 1/1 Title: Climate and Sprinkler Controller

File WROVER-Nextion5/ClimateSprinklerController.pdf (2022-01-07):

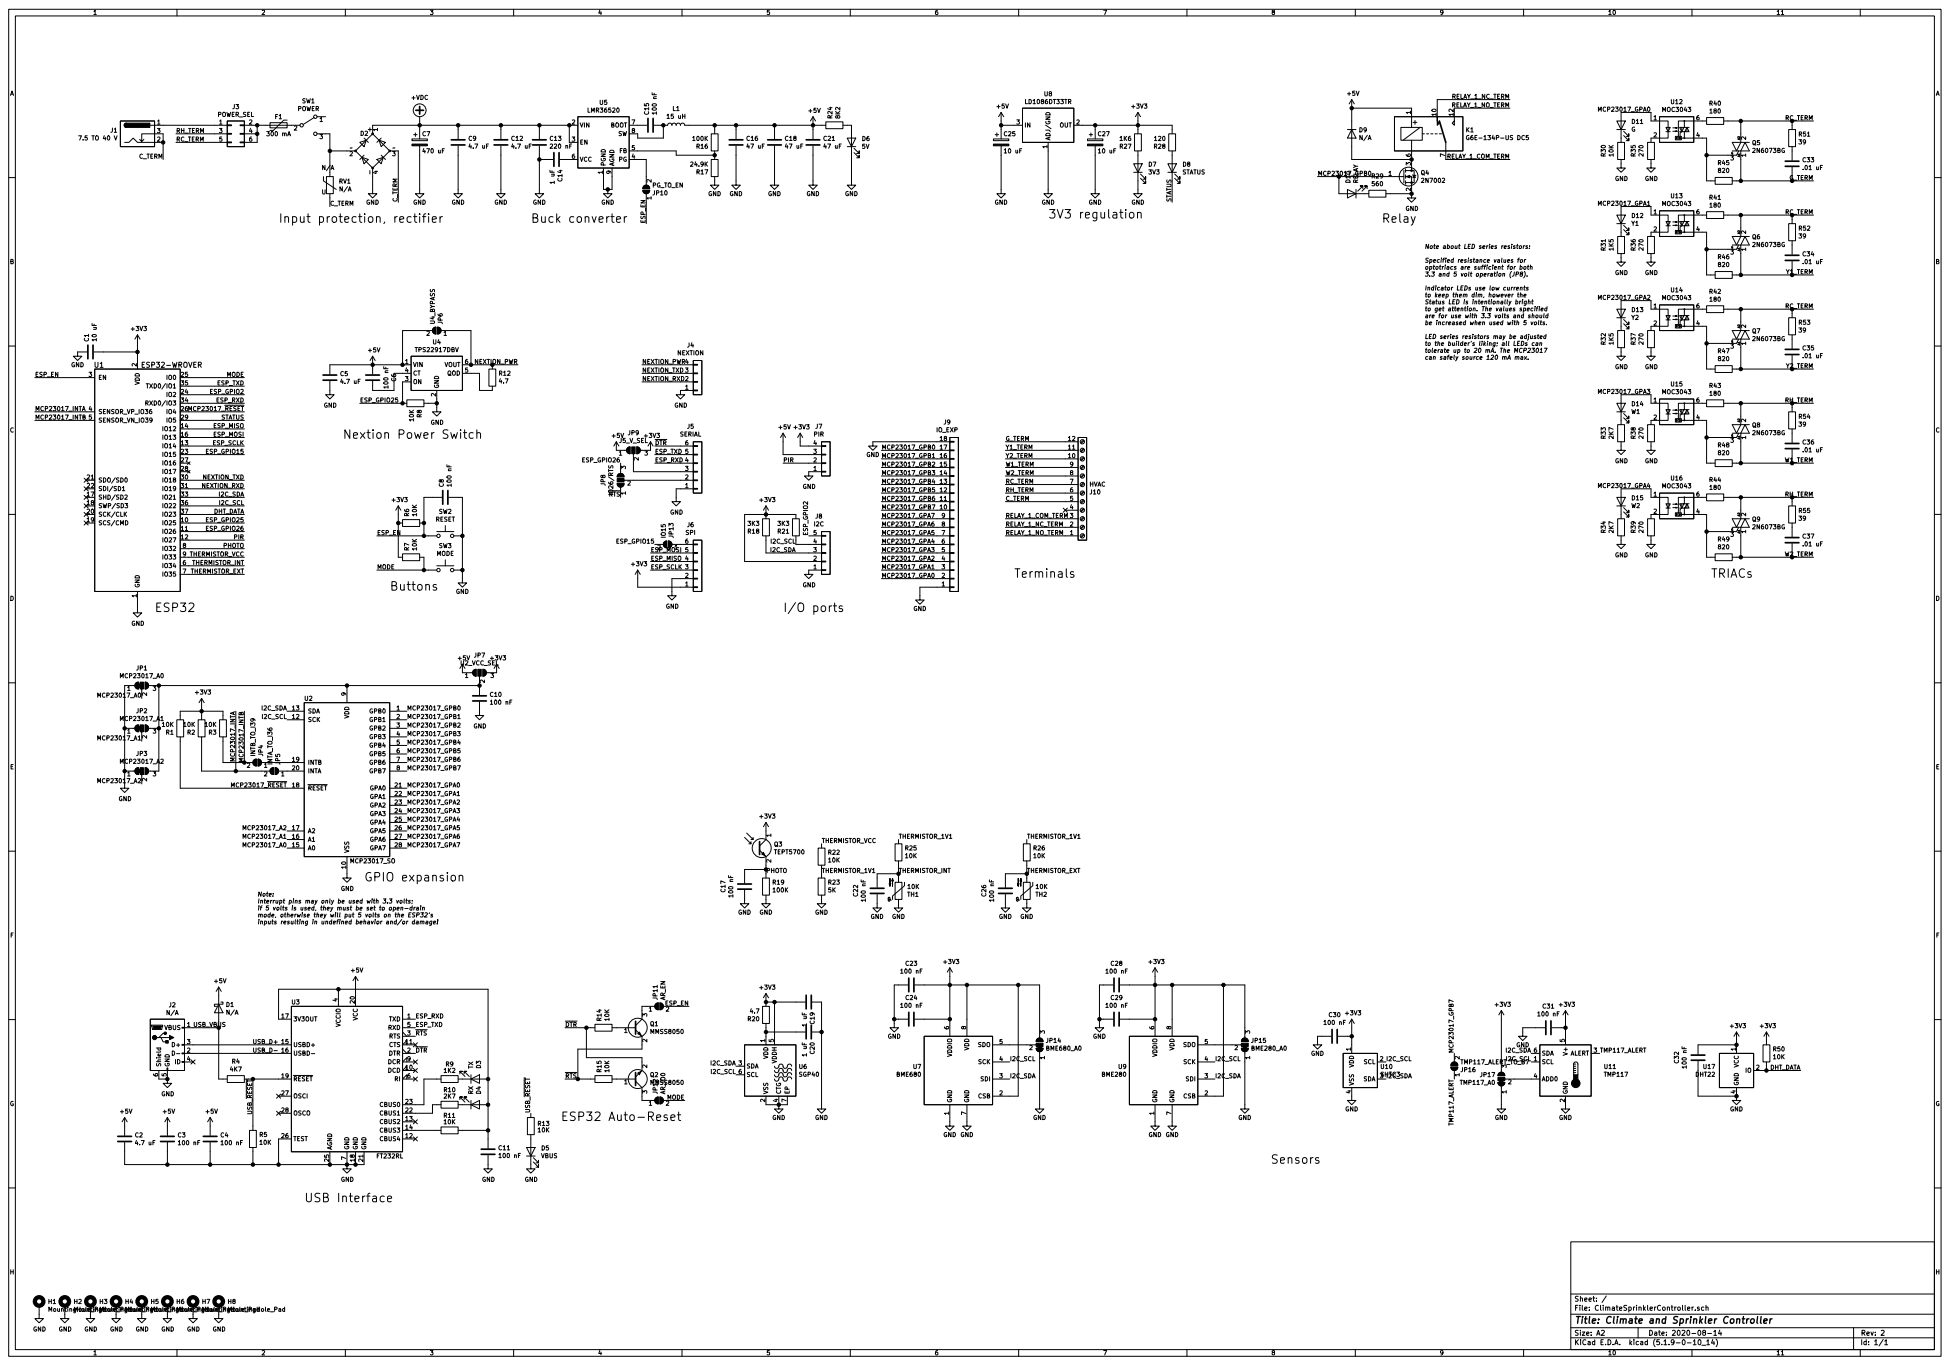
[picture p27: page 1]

1 VIN 2 EN 3 PG 4 FB 5 VCC 6 BOOT 7 SW 8 AGND

Note about LED series resistors: Specified resistance values for

optotriacs are sufficient for both
3.3 and 5 volt operation (JP8).

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

2 ON 3 CT 4 QOD 5 VOUT 6 U4 TPS22917DBV

to the builders liking; all LEDs can
tolerate up to 20 mA. The MCP23017
can safely source 120 mA max.

2 SCK/CLK 20 SDO/SD0 21 SDI/SD1 22

GND C17 100 nF D5 VBUS GND

ESP32 Auto-Reset Note:
Interrupt pins may only be used with 3.3 volts;
if 5 volts is used, they must be set to open-drain
mode, otherwise they will put 5 volts on the ESP32s
inputs resulting in undefined behavior and/or damage!

1 CSB 2 SDI 3 SCK 4 SDO 5 VDDIO

File: ClimateSprinklerController.sch Sheet: /
Id: 1/1 Title: Climate and Sprinkler Controller

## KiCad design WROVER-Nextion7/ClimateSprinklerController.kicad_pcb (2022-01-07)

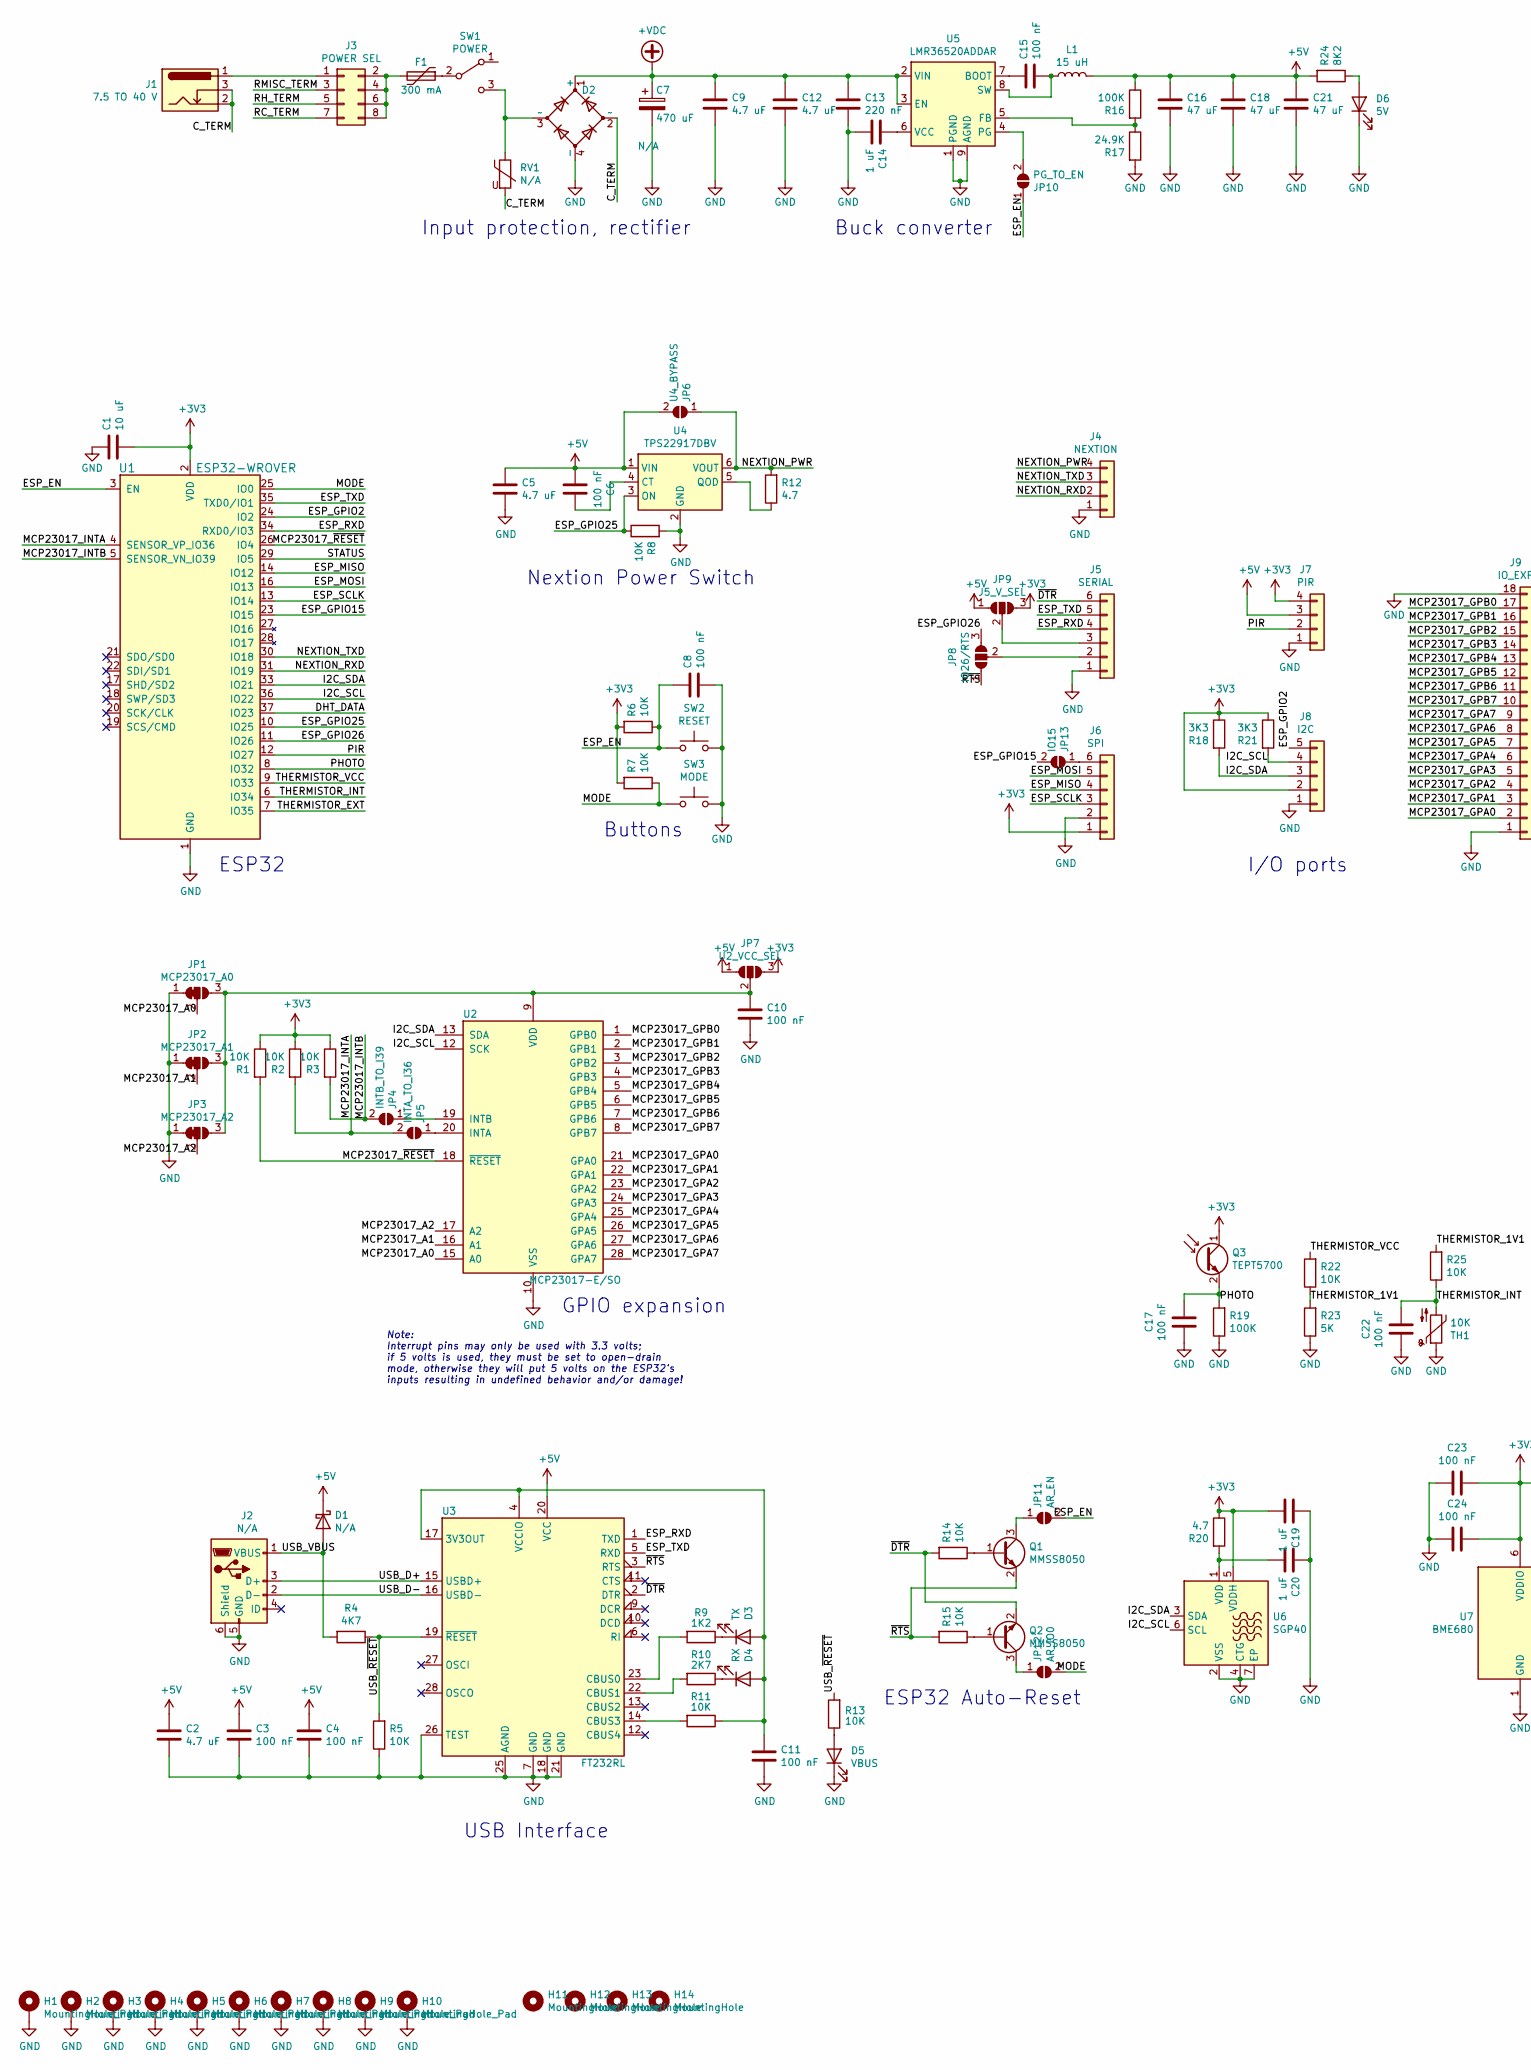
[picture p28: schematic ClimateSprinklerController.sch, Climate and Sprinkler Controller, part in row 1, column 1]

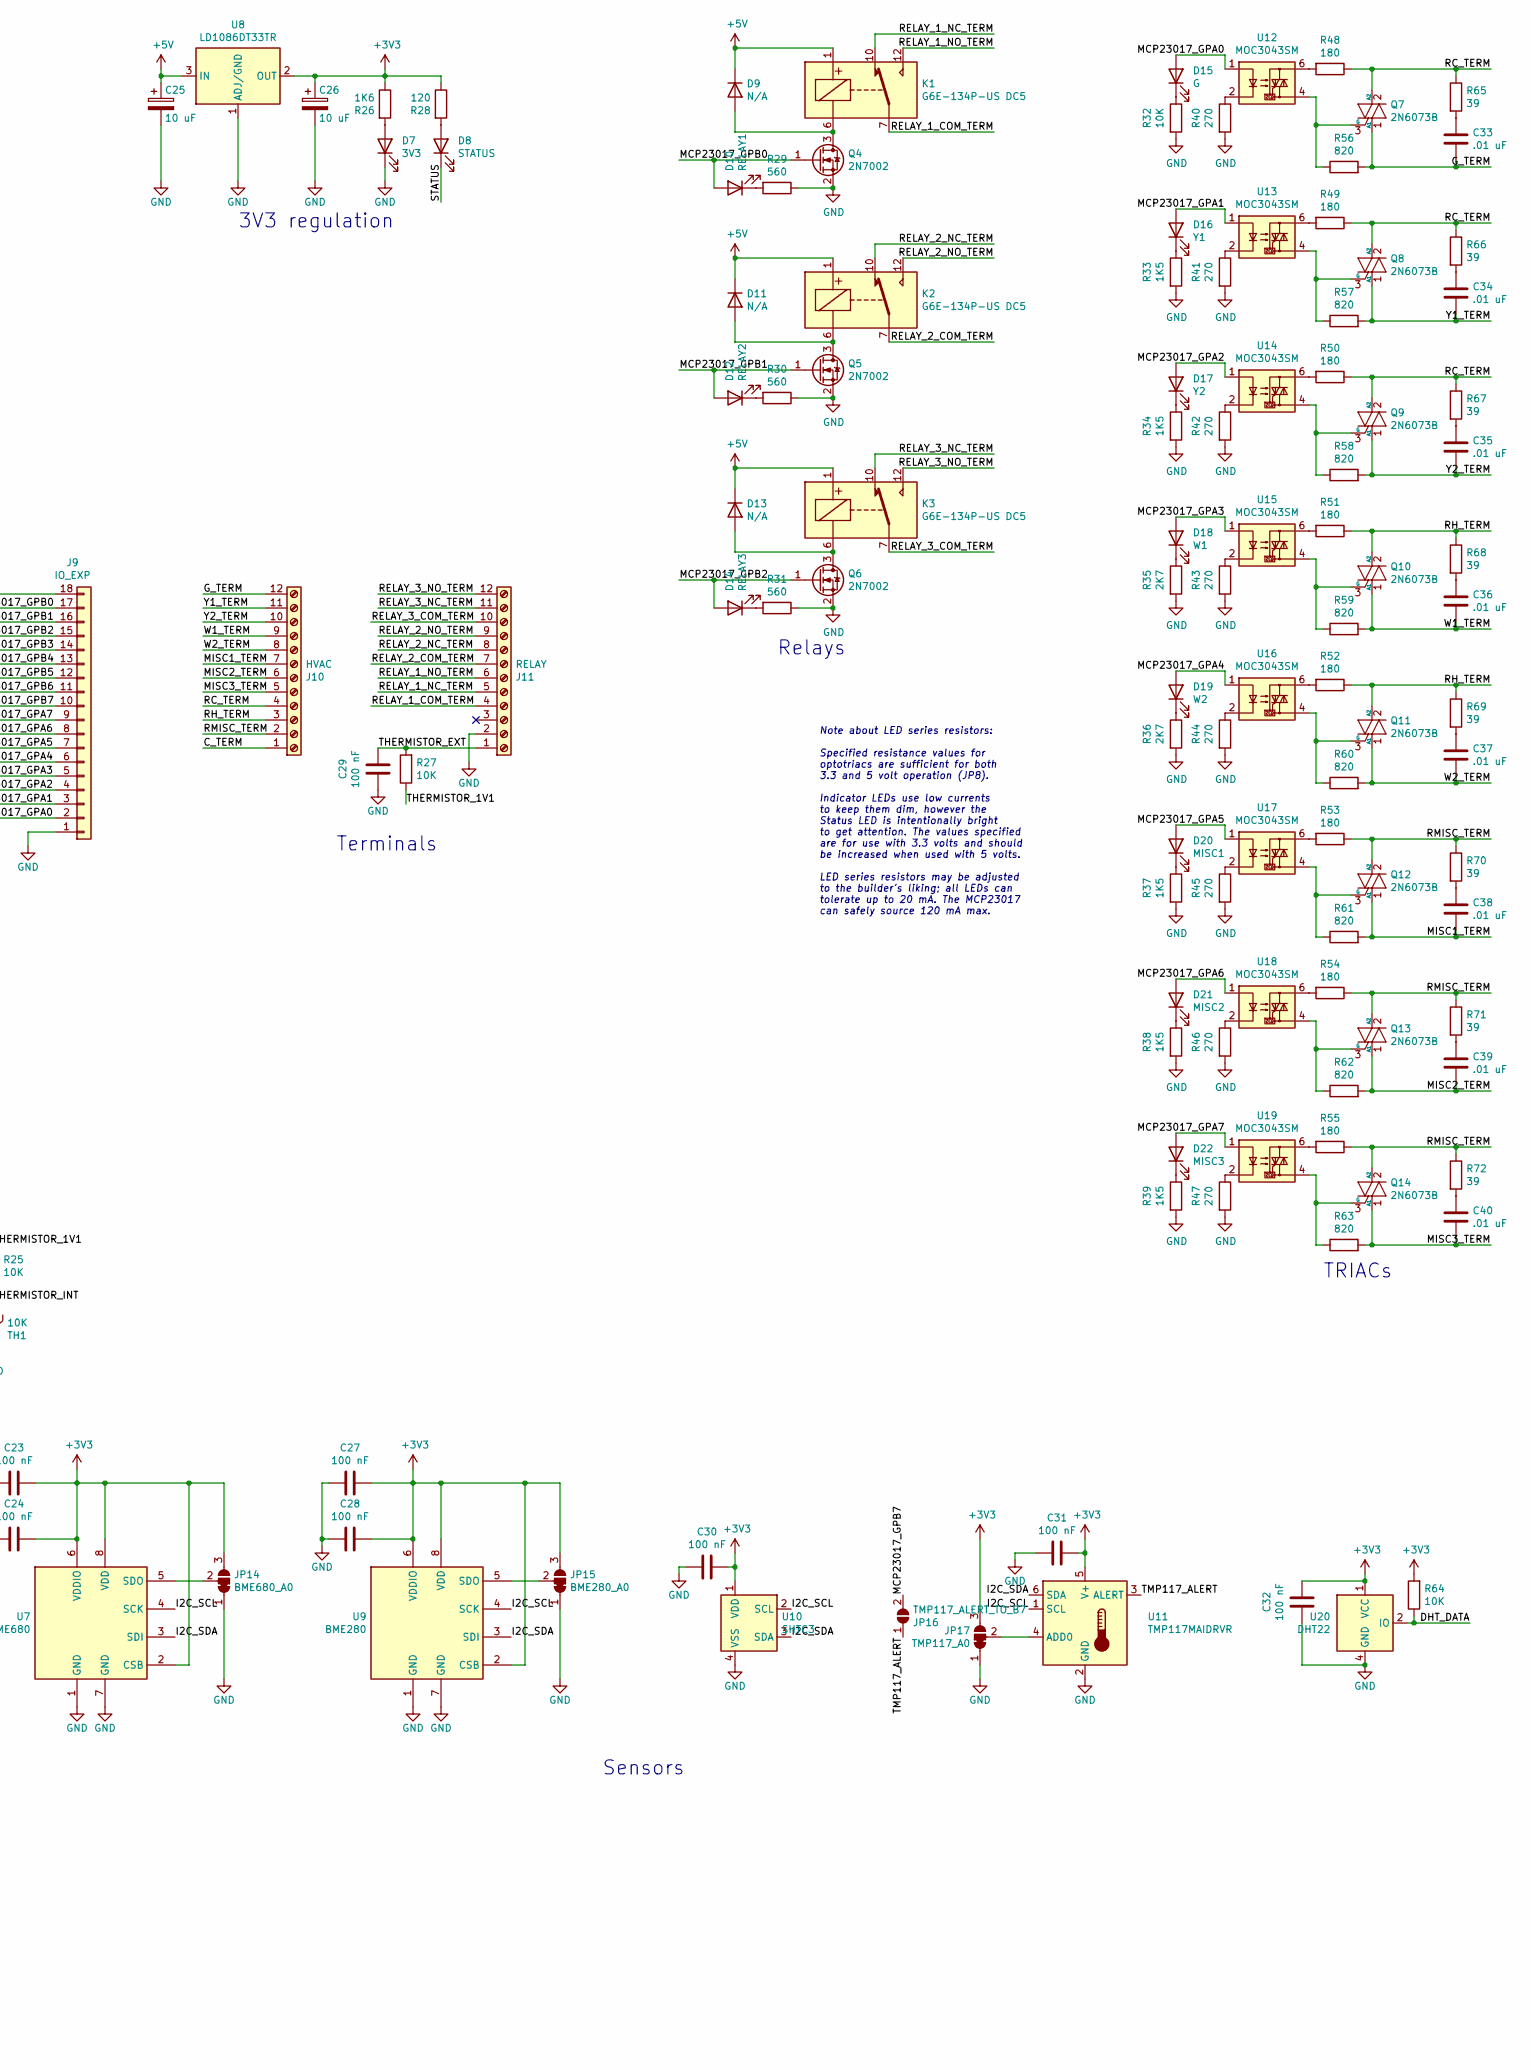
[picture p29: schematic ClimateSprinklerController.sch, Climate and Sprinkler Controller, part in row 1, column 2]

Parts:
C1: 10 uF; C_0805_2012Metric; MPN1 C2012X5R1V106K085AC
C2, C5, C9, C12: 4.7 uF; C_0805_2012Metric; MPN1 C2012X5R1H475K125AB
C3, C4, C6, C8, C10, C11, C15, C17, C22, C23, C24, C27, C28, C29, C30, C31, C32: 100 nF; C_0805_2012Metric; MPN1 CC0805KRX7R7BB104
C7: 470 uF; CP_Radial_Cutout_L20.0mm_D10.0mm_P5.00mm; MPN1 UVK1H471MPD
C13: 220 nF; C_0805_2012Metric; MPN1 C2012X5R1H224K125AA
C14, C19, C20: 1 uF; C_0805_2012Metric; MPN1 C0805C105K4RACTU
C16, C18, C21: 47 uF; C_1210_3225Metric; MPN1 GRM32ER61C476KE15L
C25, C26: 10 uF; CP_Elec_5x5.8; MPN1 EEE-HP0J100R
C33, C34, C35, C36, C37, C38, C39, C40: .01 uF; C_0805_2012Metric; MPN1 CC0805KRX7R9BB103
D1: N/A; D_SOD-123F; MPN1 MBR230S1F-7
D2: N/A; Diode_Bridge_Bourns_CD-MBL2xxS; MPN1 CD-MBL206SL
D3: TX; LED_1206_3216Metric_ReverseMount_Hole1.8x2.4mm; MPN1 APTL3216QBC/D
D4: RX; LED_1206_3216Metric_ReverseMount_Hole1.8x2.4mm; MPN1 APTL3216SURCK
D5: VBUS; LED_1206_3216Metric_ReverseMount_Hole1.8x2.4mm; MPN1 APTL3216ZGC
D6: 5V; LED_1206_3216Metric_ReverseMount_Hole1.8x2.4mm; MPN1 597-6901-607F
D7: 3V3; LED_1206_3216Metric_ReverseMount_Hole1.8x2.4mm; MPN1 597-6901-607F
D8: STATUS; LED_1206_3216Metric_ReverseMount_Hole1.8x2.4mm; MPN1 APTL3216SECK
D9, D11, D13: N/A; D_SOD-123; MPN1 1N4148W
D10: RELAY1; LED_1206_3216Metric_ReverseMount_Hole1.8x2.4mm; MPN1 APTL3216CGCK
D12: RELAY2; LED_1206_3216Metric_ReverseMount_Hole1.8x2.4mm; MPN1 APTL3216CGCK
D14: RELAY3; LED_1206_3216Metric_ReverseMount_Hole1.8x2.4mm; MPN1 APTL3216CGCK
D15: G; LED_1206_3216Metric_ReverseMount_Hole1.8x2.4mm; MPN1 APTL3216ZGC
D16: Y1; LED_1206_3216Metric_ReverseMount_Hole1.8x2.4mm; MPN1 APTL3216QBC/D
D17: Y2; LED_1206_3216Metric_ReverseMount_Hole1.8x2.4mm; MPN1 APTL3216QBC/D
D18: W1; LED_1206_3216Metric_ReverseMount_Hole1.8x2.4mm; MPN1 APTL3216SURCK
D19: W2; LED_1206_3216Metric_ReverseMount_Hole1.8x2.4mm; MPN1 APTL3216SURCK
D20: MISC1; LED_1206_3216Metric_ReverseMount_Hole1.8x2.4mm; MPN1 APTL3216SYCK
D21: MISC2; LED_1206_3216Metric_ReverseMount_Hole1.8x2.4mm; MPN1 APTL3216SYCK
D22: MISC3; LED_1206_3216Metric_ReverseMount_Hole1.8x2.4mm; MPN1 APTL3216SYCK
F1: 300 mA; Fuse_2920_7451Metric; MPN1 2920L030DR
H1, H2, H3, H4, H5, H6: MountingHole_Pad; MountingHole_3.2mm_M3_Pad_Via; MPN1 N/A
H7, H8, H9, H10: MountingHole_Pad; MountingHole_3.2mm_M3_DIN965_Pad; MPN1 N/A
H11, H12, H13, H14: MountingHole; MountingHole_4.3mm_M4_DIN965_Pad; MPN1 N/A
J1: 7.5 TO 40 V; BarrelJack_Horizontal; MPN1 694106301002
J2: N/A; USB_Micro-B_Molex-105017-0001; MPN1 105017-0001
J3: POWER SEL; PinHeader_2x04_P2.54mm_Vertical; MPN1 N/A
J4: NEXTION; PinSocket_1x04_P2.54mm_Vertical; MPN1 N/A
J5: SERIAL; PinSocket_1x06_P2.54mm_Vertical; MPN1 N/A
J6: SPI; PinSocket_1x06_P2.54mm_Vertical; MPN1 N/A
J7: PIR; PinSocket_1x04_P2.54mm_Vertical; MPN1 N/A
J8: I2C; PinSocket_1x05_P2.54mm_Vertical; MPN1 N/A
J9: IO_EXP; PinSocket_1x18_P2.54mm_Vertical; MPN1 N/A
J10: HVAC; PhoenixContact_SPTAF_1_12-3.5-IL_1x12_P3.50mm_Vertical; MPN1 1862039
J11: RELAY; PhoenixContact_SPTAF_1_12-3.5-IL_1x12_P3.50mm_Vertical; MPN1 1862039
JP1: MCP23017_A0; SolderJumper-3_P1.3mm_Bridged12_RoundedPad1.0x1.5mm; MPN1 N/A
JP2: MCP23017_A1; SolderJumper-3_P1.3mm_Bridged12_RoundedPad1.0x1.5mm; MPN1 N/A
JP3: MCP23017_A2; SolderJumper-3_P1.3mm_Bridged12_RoundedPad1.0x1.5mm; MPN1 N/A
JP4: INTB_TO_I39; SolderJumper-2_P1.3mm_Open_RoundedPad1.0x1.5mm; MPN1 N/A
JP5: INTA_TO_I36; SolderJumper-2_P1.3mm_Open_RoundedPad1.0x1.5mm; MPN1 N/A
JP6: U4_BYPASS; SolderJumper-2_P1.3mm_Open_RoundedPad1.0x1.5mm; MPN1 N/A
JP7: U2_VCC_SEL; SolderJumper-3_P1.3mm_Open_RoundedPad1.0x1.5mm; MPN1 N/A
JP8: IO26/RTS; SolderJumper-3_P1.3mm_Open_RoundedPad1.0x1.5mm; MPN1 N/A
JP9: J5_V_SEL; SolderJumper-3_P1.3mm_Open_RoundedPad1.0x1.5mm; MPN1 N/A
JP10: PG_TO_EN; SolderJumper-2_P1.3mm_Open_RoundedPad1.0x1.5mm; MPN1 N/A
JP11: AR_EN; SolderJumper-2_P1.3mm_Open_RoundedPad1.0x1.5mm; MPN1 N/A
JP12: AR_IO0; SolderJumper-2_P1.3mm_Open_RoundedPad1.0x1.5mm; MPN1 N/A
JP13: IO15; SolderJumper-2_P1.3mm_Open_RoundedPad1.0x1.5mm; MPN1 N/A
JP14: BME680_A0; SolderJumper-3_P1.3mm_Bridged12_RoundedPad1.0x1.5mm; MPN1 N/A
JP15: BME280_A0; SolderJumper-3_P1.3mm_Bridged12_RoundedPad1.0x1.5mm; MPN1 N/A
JP16: TMP117_ALERT_TO_B7; SolderJumper-2_P1.3mm_Open_RoundedPad1.0x1.5mm; MPN1 N/A
JP17: TMP117_A0; SolderJumper-3_P1.3mm_Bridged12_RoundedPad1.0x1.5mm; MPN1 N/A
K1, K2, K3: G6E-134P-US DC5; Relay_SPDT_Omron_G6E; MPN1 G6E-134P-US DC5
L1: 15 uH; L_Wuerth_WE-PD-Typ-LS; MPN1 7447709150
Q1, Q2: MMSS8050; SOT-23; MPN1 MMSS8050
Q3: TEPT5700; LED_D5.0mm_Clear; MPN1 TEPT5700
Q4, Q5, Q6: 2N7002; SOT-23; MPN1 2N7002
Q7, Q8, Q9, Q10, Q11, Q12, Q13, Q14: 2N6073B; TO-225-3_Vertical; MPN1 2N6073BG
R1, R2, R3, R5, R6, R7, R8, R11, R13, R14, R15, R22, R25, R27, R32, R64: 10K; R_0805_2012Metric_Pad1.20x1.40mm_HandSolder; MPN1 RC0805FR-0710KL
R4: 4K7; R_0805_2012Metric_Pad1.20x1.40mm_HandSolder; MPN1 RT0805FRE074K7L
R9: 1K2; R_0805_2012Metric_Pad1.20x1.40mm_HandSolder; MPN1 RT0805FRE072K7L
R10, R35, R36: 2K7; R_0805_2012Metric_Pad1.20x1.40mm_HandSolder; MPN1 RT0805FRE072K7L
R12, R20: 4.7; R_0805_2012Metric_Pad1.20x1.40mm_HandSolder; MPN1 RC0805FR-074R7L
R16, R19: 100K; R_0805_2012Metric_Pad1.20x1.40mm_HandSolder; MPN1 RC0805FR-07100KL
R17: 24.9K; R_0805_2012Metric_Pad1.20x1.40mm_HandSolder; MPN1 RT0805FRE0724K9L
R18, R21: 3K3; R_0805_2012Metric_Pad1.20x1.40mm_HandSolder; MPN1 RT0805FRE073K3L
R23: 5K; R_0805_2012Metric_Pad1.20x1.40mm_HandSolder; MPN1 CRCW08055K00JNTA
R24: 8K2; R_0805_2012Metric_Pad1.20x1.40mm_HandSolder; MPN1 RT0805FRE078K2L
R26: 1K6; R_0805_2012Metric_Pad1.20x1.40mm_HandSolder; MPN1 RT0805FRE071K6L
R28: 120; R_0805_2012Metric_Pad1.20x1.40mm_HandSolder; MPN1 RT0805FRE07120RL
R29, R30, R31: 560; R_0805_2012Metric_Pad1.20x1.40mm_HandSolder; MPN1 RT0805FRE07560RL
R33, R34, R37, R38, R39: 1K5; R_0805_2012Metric_Pad1.20x1.40mm_HandSolder; MPN1 RT0805FRE071K5L
R40, R41, R42, R43, R44, R45, R46, R47: 270; R_0805_2012Metric_Pad1.20x1.40mm_HandSolder; MPN1 RT0805FRE07270RL
R48, R49, R50, R51, R52, R53, R54, R55: 180; R_0805_2012Metric_Pad1.20x1.40mm_HandSolder; MPN1 RT0805FRE07180RL
R56, R57, R58, R59, R60, R61, R62, R63: 820; R_0805_2012Metric_Pad1.20x1.40mm_HandSolder; MPN1 RT0805FRE07820RL
R65, R66, R67, R68, R69, R70, R71, R72: 39; R_0805_2012Metric_Pad1.20x1.40mm_HandSolder; MPN1 ERJ-P06J390V
RV1: N/A; RV_Disc_D7mm_W4mm_P5mm; MPN1 B72205S0400K101
SW1: POWER; SW_Push_1P2T_Vertical_E-Switch_800UDP8P1A1M6; MPN1 48BFSP1M6QT
SW2: RESET; SW_Tactile_SPST_Angled_PTS645Vx58-2LFS; MPN1 PTS645VK582LFS
SW3: MODE; SW_Tactile_SPST_Angled_PTS645Vx58-2LFS; MPN1 PTS645VK582LFS
TH1: 10K; PinSocket_1x02_P2.54mm_Vertical; MPN1 NXFT15XH103FA2B100
U1: ESP32-WROVER; MPN1 ESP32-WROVER
U2: MCP23017-E/SO; SOIC-28W_7.5x17.9mm_P1.27mm; MPN1 MCP23017-E/SO
U3: FT232RL; SSOP-28_5.3x10.2mm_P0.65mm; MPN1 FT232RL
U4: TPS22917DBV; SOT-23-6; MPN1 TPS22917DBV
U5: LMR36520ADDAR; Texas_HSOP-8-1EP_3.9x4.9mm_P1.27mm_ThermalVias; MPN1 LMR36520ADDAR
U6: SGP40; DFN-6-1EP_2.44x2.44mm_P0.8mm_EP1.25x1.7mm; MPN1 SGP40
U7: BME680; Bosch_LGA-8_3x3mm_P0.8mm_ClockwisePinNumbering; MPN1 BME680
U8: LD1086DT33TR; TO-252-2; MPN1 LD1086DT33TR
U9: BME280; Bosch_LGA-8_2.5x2.5mm_P0.65mm_ClockwisePinNumbering; MPN1 BME280
U10: SHTC3; AMS_QFN-4-1EP_2x2mm_P0.95mm_EP0.7x1.6mm; MPN1 SHTC3
U11: TMP117MAIDRVR; WSON-6-1EP_2x2mm_P0.65mm_EP1x1.6mm; MPN1 TMP117MAIDRVR
U12, U13, U14, U15, U16, U17, U18, U19: MOC3043SM; SMDIP-6_W9.53mm; MPN1 MOC3043SM
U20: DHT22; PinSocket_1x04_P2.54mm_Vertical; MPN1 DHT22

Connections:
+3V3: C1.2, C19.2, C23.1, C24.1, C26.1, C27.1, C28.1, C30.1, C31.1, C32.1, J6.1, J7.4, J8.2, JP7.3 (B), JP9.3 (B), JP14.3 (B), JP15.3 (B), JP17.3 (B), Q3.1 (C), R1.1, R2.1, R3.1, R6.2, R7.2, R18.1, R20.1, R21.1, R26.1, R28.1, R64.2, U1.2 (VDD), U6.5 (VDDH), U7.2 (CSB), U7.6 (VDDIO), U7.8 (VDD), U8.2 (OUT), U9.2 (CSB), U9.6 (VDDIO), U9.8 (VDD), U10.1 (VDD), U11.5 (V+), U20.1 (VCC)
+5V: C2.1, C3.1, C4.1, C5.1, C6.2, C16.1, C18.1, C21.1, C25.1, D1.1 (K), D9.1 (K), D11.1 (K), D13.1 (K), J7.3, JP6.2 (B), JP7.1 (A), JP9.1 (A), K1.1, K2.1, K3.1, L1.2, R16.1, R24.2, U3.20 (VCC), U4.1 (VIN), U8.3 (IN)
+VDC: C7.1, C9.1, C12.1, C13.1, D2.1 (+), U5.2 (VIN), U5.3 (EN)
/C_TERM: D2.2 (~~), J1.2, J1.3, J10.1, RV1.2
/DHT_DATA: R64.1, U1.37 (IO23), U20.2 (IO)
/ESP_EN: C8.1, JP10.1 (A), JP11.2 (B), R6.1, SW2.2, U1.3 (EN)
/ESP_GPIO2: J8.5, U1.24 (IO2)
/ESP_GPIO15: JP13.2 (B), U1.23 (IO15)
/ESP_GPIO25: R8.1, U1.10 (IO25), U4.3 (ON)
/ESP_GPIO26: JP8.3 (B), U1.11 (IO26)
/ESP_MISO: J6.4, U1.14 (IO12)
/ESP_MOSI: J6.5, U1.16 (IO13)
/ESP_RXD: J5.4, U1.34 (RXD0/IO3), U3.1 (TXD)
/ESP_SCLK: J6.3, U1.13 (IO14)
/ESP_TXD: J5.5, U1.35 (TXD0/IO1), U3.5 (RXD)
/G_TERM: C33.2, J10.12, Q7.1 (A1), R56.2
/I2C_SCL: J8.4, R21.2, U1.36 (IO22), U2.12 (SCK), U6.6 (SCL), U7.4 (SCK), U9.4 (SCK), U10.2 (SCL), U11.1 (SCL)
/I2C_SDA: J8.3, R18.2, U1.33 (IO21), U2.13 (SDA), U6.3 (SDA), U7.3 (SDI), U9.3 (SDI), U10.3 (SDA), U11.6 (SDA)
/MCP23017_A0: JP1.2 (C), U2.15 (A0)
/MCP23017_A1: JP2.2 (C), U2.16 (A1)
/MCP23017_A2: JP3.2 (C), U2.17 (A2)
/MCP23017_GPA0: D15.2 (A), J9.2, U2.21 (GPA0), U12.1
/MCP23017_GPA1: D16.2 (A), J9.3, U2.22 (GPA1), U13.1
/MCP23017_GPA2: D17.2 (A), J9.4, U2.23 (GPA2), U14.1
/MCP23017_GPA3: D18.2 (A), J9.5, U2.24 (GPA3), U15.1
/MCP23017_GPA4: D19.2 (A), J9.6, U2.25 (GPA4), U16.1
/MCP23017_GPA5: D20.2 (A), J9.7, U2.26 (GPA5), U17.1
/MCP23017_GPA6: D21.2 (A), J9.8, U2.27 (GPA6), U18.1
/MCP23017_GPA7: D22.2 (A), J9.9, U2.28 (GPA7), U19.1
/MCP23017_GPB0: D10.2 (A), J9.17, Q4.1 (G), U2.1 (GPB0)
/MCP23017_GPB1: D12.2 (A), J9.16, Q5.1 (G), U2.2 (GPB1)
/MCP23017_GPB2: D14.2 (A), J9.15, Q6.1 (G), U2.3 (GPB2)
/MCP23017_GPB3: J9.14, U2.4 (GPB3)
/MCP23017_GPB4: J9.13, U2.5 (GPB4)
/MCP23017_GPB5: J9.12, U2.6 (GPB5)
/MCP23017_GPB6: J9.11, U2.7 (GPB6)
/MCP23017_GPB7: J9.10, JP16.2 (B), U2.8 (GPB7)
/MCP23017_INTA: JP5.2 (B), R2.2, U1.4 (SENSOR_VP_IO36)
/MCP23017_INTB: JP4.2 (B), R3.2, U1.5 (SENSOR_VN_IO39)
/MCP23017_~RESET: R1.2, U1.26 (IO4), U2.18 (~RESET~)
/MISC1_TERM: C38.2, J10.7, Q12.1 (A1), R61.2
/MISC2_TERM: C39.2, J10.6, Q13.1 (A1), R62.2
/MISC3_TERM: C40.2, J10.5, Q14.1 (A1), R63.2
/MODE: JP12.2 (B), R7.1, SW3.1, U1.25 (IO0)
/NEXTION_PWR: J4.4, JP6.1 (A), R12.2, U4.6 (VOUT)
/NEXTION_RXD: J4.2, U1.31 (IO19)
/NEXTION_TXD: J4.3, U1.30 (IO18)
/PHOTO: C17.1, Q3.2 (E), R19.2, U1.8 (IO32)
/PIR: J7.2, U1.12 (IO27)
/RC_TERM: J3.7, J10.4, Q7.2 (A2), Q8.2 (A2), Q9.2 (A2), R48.1, R49.1, R50.1, R65.1, R66.1, R67.1
/RELAY_1_COM_TERM: J11.4, K1.7
/RELAY_1_NC_TERM: J11.5, K1.10
/RELAY_1_NO_TERM: J11.6, K1.12
/RELAY_2_COM_TERM: J11.7, K2.7
/RELAY_2_NC_TERM: J11.8, K2.10
/RELAY_2_NO_TERM: J11.9, K2.12
/RELAY_3_COM_TERM: J11.10, K3.7
/RELAY_3_NC_TERM: J11.11, K3.10
/RELAY_3_NO_TERM: J11.12, K3.12
/RH_TERM: J3.5, J10.3, Q10.2 (A2), Q11.2 (A2), R51.1, R52.1, R68.1, R69.1
/RMISC_TERM: J3.3, J10.2, Q12.2 (A2), Q13.2 (A2), Q14.2 (A2), R53.1, R54.1, R55.1, R70.1, R71.1, R72.1
/STATUS: D8.1 (K), U1.29 (IO5)
/THERMISTOR_1V1: R22.1, R23.2, R25.2, R27.1
/THERMISTOR_EXT: C29.1, J11.1, R27.2, U1.7 (IO35)
/THERMISTOR_INT: C22.1, R25.1, TH1.2, U1.6 (IO34)
/THERMISTOR_VCC: R22.2, U1.9 (IO33)
/TMP117_ALERT: JP16.1 (A), U11.3 (ALERT)
/USB_D+: J2.3 (D+), U3.15 (USBD+)
/USB_D-: J2.2 (D-), U3.16 (USBD-)
/USB_VBUS: D1.2 (A), J2.1 (VBUS), R4.2
/USB_~RESET: R4.1, R5.2, R13.2, U3.19 (~RESET~)
/W1_TERM: C36.2, J10.9, Q10.1 (A1), R59.2
/W2_TERM: C37.2, J10.8, Q11.1 (A1), R60.2
/Y1_TERM: C34.2, J10.11, Q8.1 (A1), R57.2
/Y2_TERM: C35.2, J10.10, Q9.1 (A1), R58.2
/~DTR: J5.6, Q2.2 (E), R14.2, U3.2 (DTR)
/~RTS: JP8.1 (A), Q1.2 (E), R15.2, U3.3 (RTS)
GND: C1.1, C2.2, C3.2, C4.2, C5.2, C7.2, C8.2, C9.2, C10.2, C11.2, C12.2, C13.2, C14.2, C16.2, C17.2, C18.2, C19.1, C20.1, C21.2, C22.2, C23.2, C24.2, C25.2, C26.2, C27.2, C28.2, C29.2, C30.2, C31.2, C32.2, D2.4 (-), D5.1 (K), D6.1 (K), D7.1 (K), H1.1, H2.1, H3.1, H4.1, H5.1, H6.1, H7.1, H8.1, H9.1, H10.1, J2.5 (GND), J2.6 (Shield), J4.1, J5.1, J6.2, J7.1, J8.1, J9.1, J9.18, J11.2, JP1.1 (A), JP2.1 (A), JP3.1 (A), JP14.1 (A), JP15.1 (A), JP17.1 (A), Q4.2 (S), Q5.2 (S), Q6.2 (S), R5.1, R8.2, R17.2, R19.1, R23.1, R29.1, R30.1, R31.1, R32.2, R33.2, R34.2, R35.2, R36.2, R37.2, R38.2, R39.2, R40.2, R41.2, R42.2, R43.2, R44.2, R45.2, R46.2, R47.2, SW2.1, SW3.2, TH1.1, U1.1 (GND), U1.15 (GND), U1.38 (GND), U1.39 (GND), U2.10 (VSS), U3.7 (GND), U3.18 (GND), U3.21 (GND), U3.25 (AGND), U3.26 (TEST), U4.2 (GND), U5.1 (PGND), U5.9 (AGND), U6.2 (VSS), U6.4 (CTG), U6.7 (EP), U7.1 (GND), U7.7 (GND), U8.1 (ADJ/GND), U9.1 (GND), U9.7 (GND), U10.4 (VSS), U11.2 (GND), U20.4 (GND)
unnamed: C6.1, U4.4 (CT)
unnamed: C10.1, JP1.3 (B), JP2.3 (B), JP3.3 (B), JP7.2 (C), U2.9 (VDD)
unnamed: C11.1, D3.2 (A), D4.2 (A), R11.1, U3.4 (VCCIO), U3.17 (3V3OUT)
unnamed: C14.1, U5.6 (VCC)
unnamed: C15.1, U5.7 (BOOT)
unnamed: C15.2, L1.1, U5.8 (SW)
unnamed: C20.2, R20.2, U6.1 (VDD)
unnamed: C33.1, R65.2
unnamed: C34.1, R66.2
unnamed: C35.1, R67.2
unnamed: C36.1, R68.2
unnamed: C37.1, R69.2
unnamed: C38.1, R70.2
unnamed: C39.1, R71.2
unnamed: C40.1, R72.2
unnamed: D2.3 (~~), RV1.1, SW1.3 (C)
unnamed: D3.1 (K), R9.1
unnamed: D4.1 (K), R10.1
unnamed: D5.2 (A), R13.1
unnamed: D6.2 (A), R24.1
unnamed: D7.2 (A), R26.2
unnamed: D8.2 (A), R28.2
unnamed: D9.2 (A), K1.6, Q4.3 (D)
unnamed: D10.1 (K), R29.2
unnamed: D11.2 (A), K2.6, Q5.3 (D)
unnamed: D12.1 (K), R30.2
unnamed: D13.2 (A), K3.6, Q6.3 (D)
unnamed: D14.1 (K), R31.2
unnamed: D15.1 (K), R32.1
unnamed: D16.1 (K), R33.1
unnamed: D17.1 (K), R34.1
unnamed: D18.1 (K), R35.1
unnamed: D19.1 (K), R36.1
unnamed: D20.1 (K), R37.1
unnamed: D21.1 (K), R38.1
unnamed: D22.1 (K), R39.1
unnamed: F1.1, SW1.2 (B)
unnamed: F1.2, J3.2, J3.4, J3.6, J3.8
unnamed: J1.1, J3.1
unnamed: J5.2, JP8.2 (C)
unnamed: J5.3, JP9.2 (C)
unnamed: J6.6, JP13.1 (A)
unnamed: JP4.1 (A), U2.19 (INTB)
unnamed: JP5.1 (A), U2.20 (INTA)
unnamed: JP10.2 (B), U5.4 (PG)
unnamed: JP11.1 (A), Q1.3 (C)
unnamed: JP12.1 (A), Q2.3 (C)
unnamed: JP14.2 (C), U7.5 (SDO)
unnamed: JP15.2 (C), U9.5 (SDO)
unnamed: JP17.2 (C), U11.4 (ADD0)
unnamed: Q1.1 (B), R14.1
unnamed: Q2.1 (B), R15.1
unnamed: Q7.3 (G), R56.1, U12.4
unnamed: Q8.3 (G), R57.1, U13.4
unnamed: Q9.3 (G), R58.1, U14.4
unnamed: Q10.3 (G), R59.1, U15.4
unnamed: Q11.3 (G), R60.1, U16.4
unnamed: Q12.3 (G), R61.1, U17.4
unnamed: Q13.3 (G), R62.1, U18.4
unnamed: Q14.3 (G), R63.1, U19.4
unnamed: R9.2, U3.23 (CBUS0)
unnamed: R10.2, U3.22 (CBUS1)
unnamed: R11.2, U3.14 (CBUS3)
unnamed: R12.1, U4.5 (QOD)
unnamed: R16.2, R17.1, U5.5 (FB)
unnamed: R40.1, U12.2
unnamed: R41.1, U13.2
unnamed: R42.1, U14.2
unnamed: R43.1, U15.2
unnamed: R44.1, U16.2
unnamed: R45.1, U17.2
unnamed: R46.1, U18.2
unnamed: R47.1, U19.2
unnamed: R48.2, U12.6
unnamed: R49.2, U13.6
unnamed: R50.2, U14.6
unnamed: R51.2, U15.6
unnamed: R52.2, U16.6
unnamed: R53.2, U17.6
unnamed: R54.2, U18.6
unnamed: R55.2, U19.6

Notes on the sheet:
Buck converter
3V3 regulation
Relays
TRIACs
Terminals
I/O ports
ESP32
GPIO expansion
Buttons
Input protection, rectifier
Note: Interrupt pins may only be used with 3.3 volts; if 5 volts is used, they must be set to open-drain mode, otherwise they will put 5 volts on the ESP32’s inputs resulting in undefined behavior and/or damage!
Note about LED series resistors: Specified resistance values for optotriacs are sufficient for both 3.3 and 5 volt operation (JP8). Indicator LEDs use low currents to keep them dim, however the Status LED is intentionally bright to get attention. The values specified are for use with 3.3 volts and 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
Sensors
ESP32 Auto-Reset
USB Interface
Nextion Power Switch

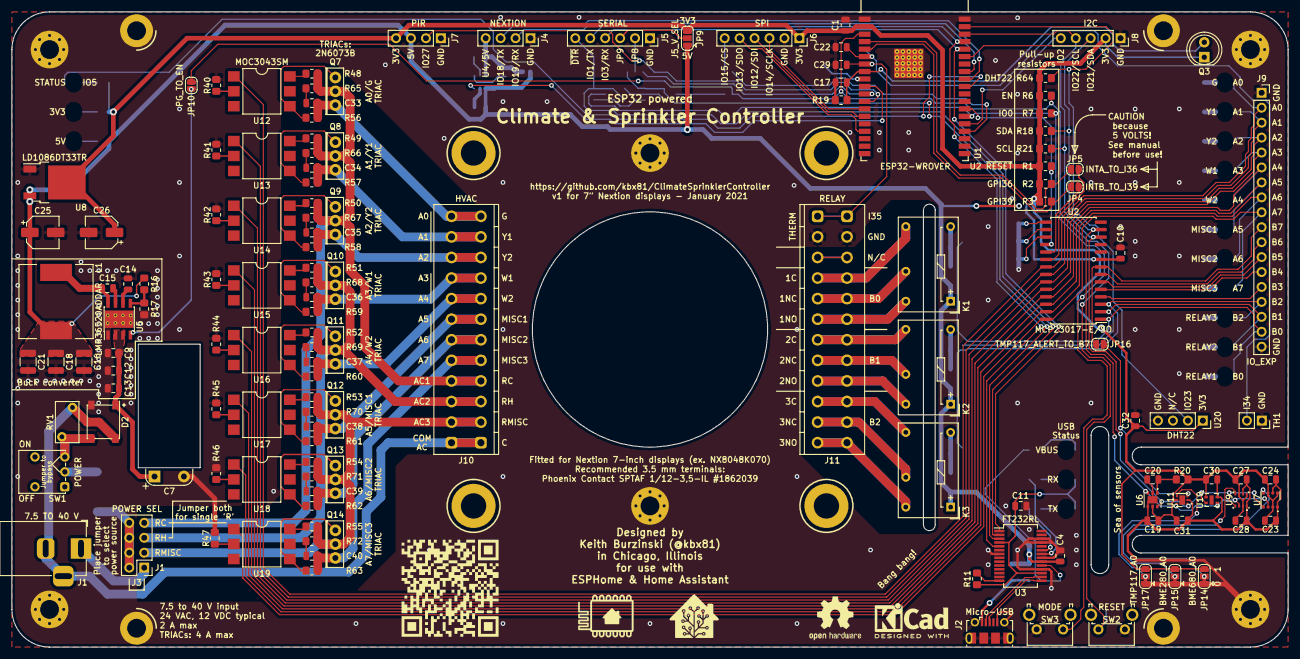
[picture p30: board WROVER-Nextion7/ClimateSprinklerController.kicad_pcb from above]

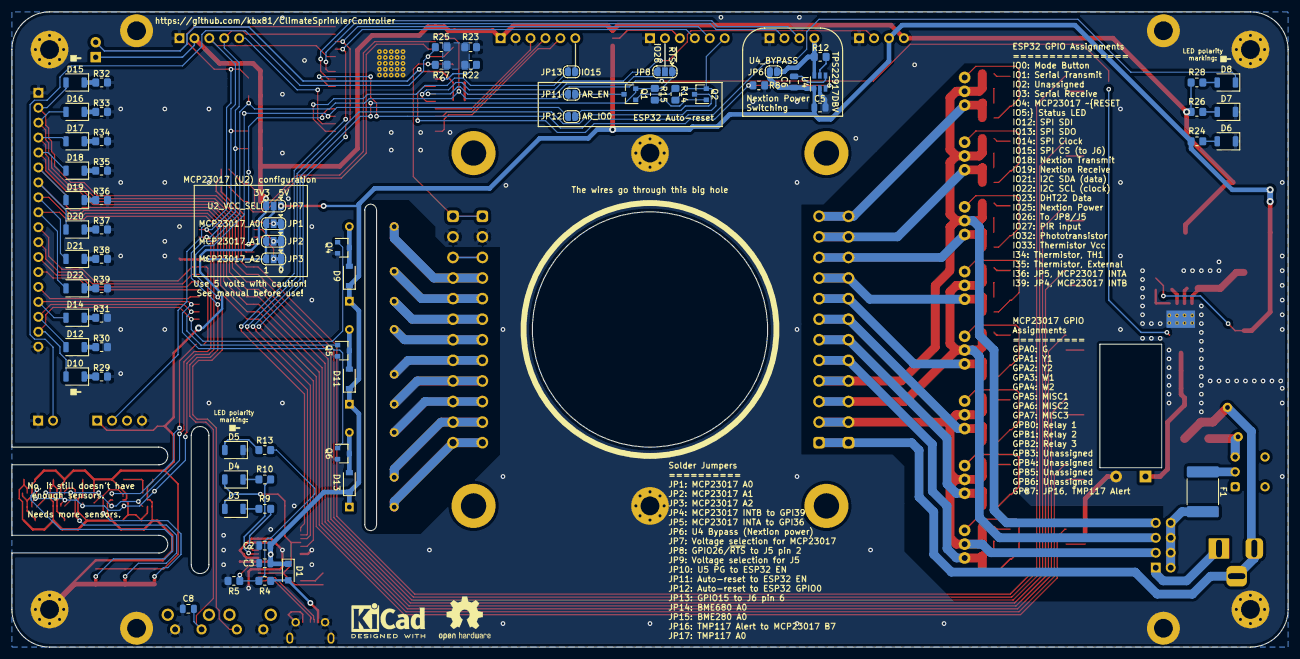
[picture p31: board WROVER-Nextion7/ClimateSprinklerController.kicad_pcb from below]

Board: 2 copper layers, 217.0 x 108.0 mm, 221 parts (69 on the bottom side), 159 nets.

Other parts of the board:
QR*****: ClimateSprinklerControllerQR

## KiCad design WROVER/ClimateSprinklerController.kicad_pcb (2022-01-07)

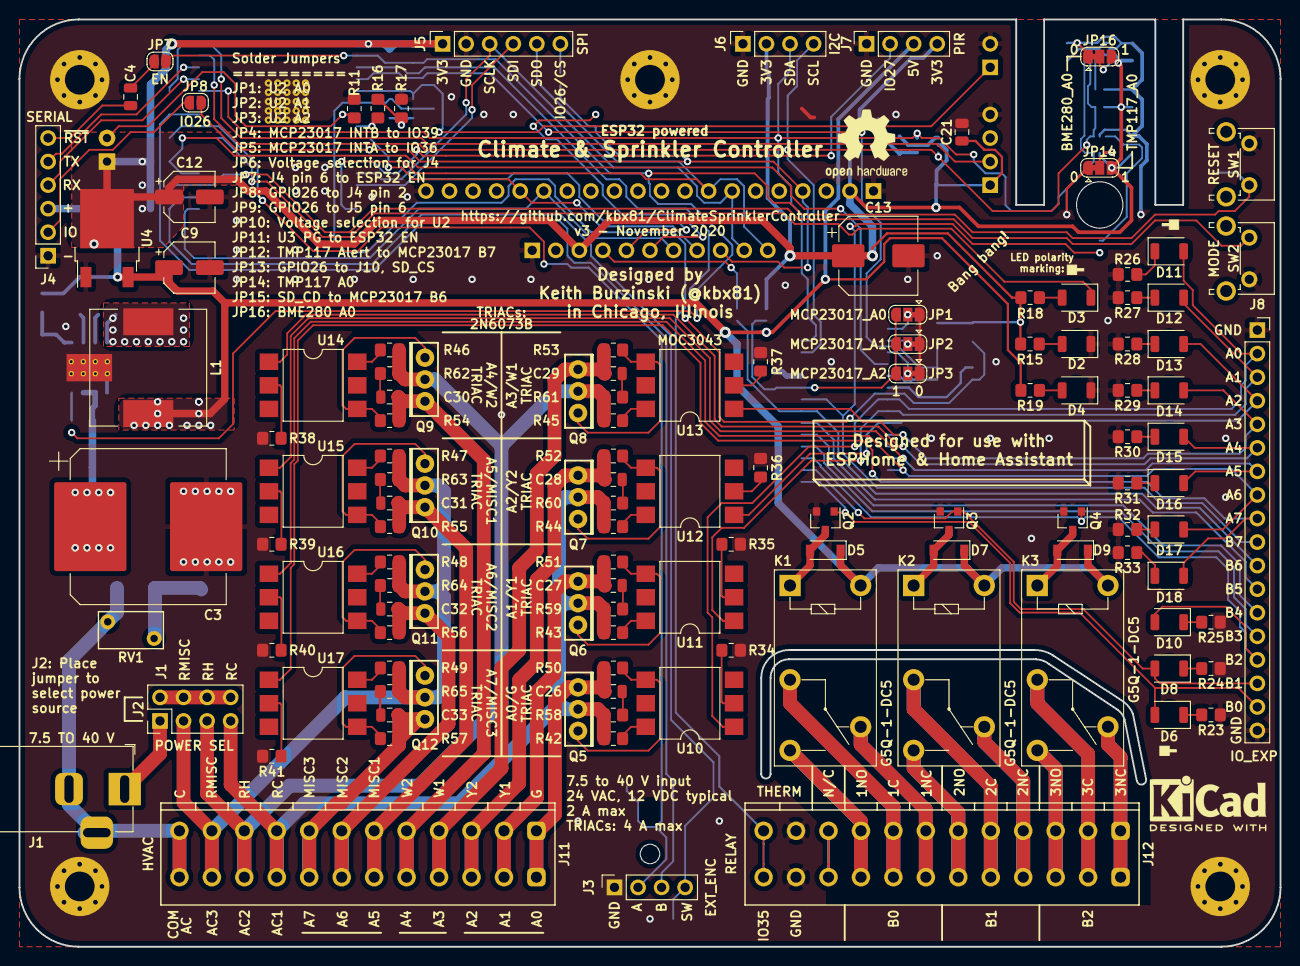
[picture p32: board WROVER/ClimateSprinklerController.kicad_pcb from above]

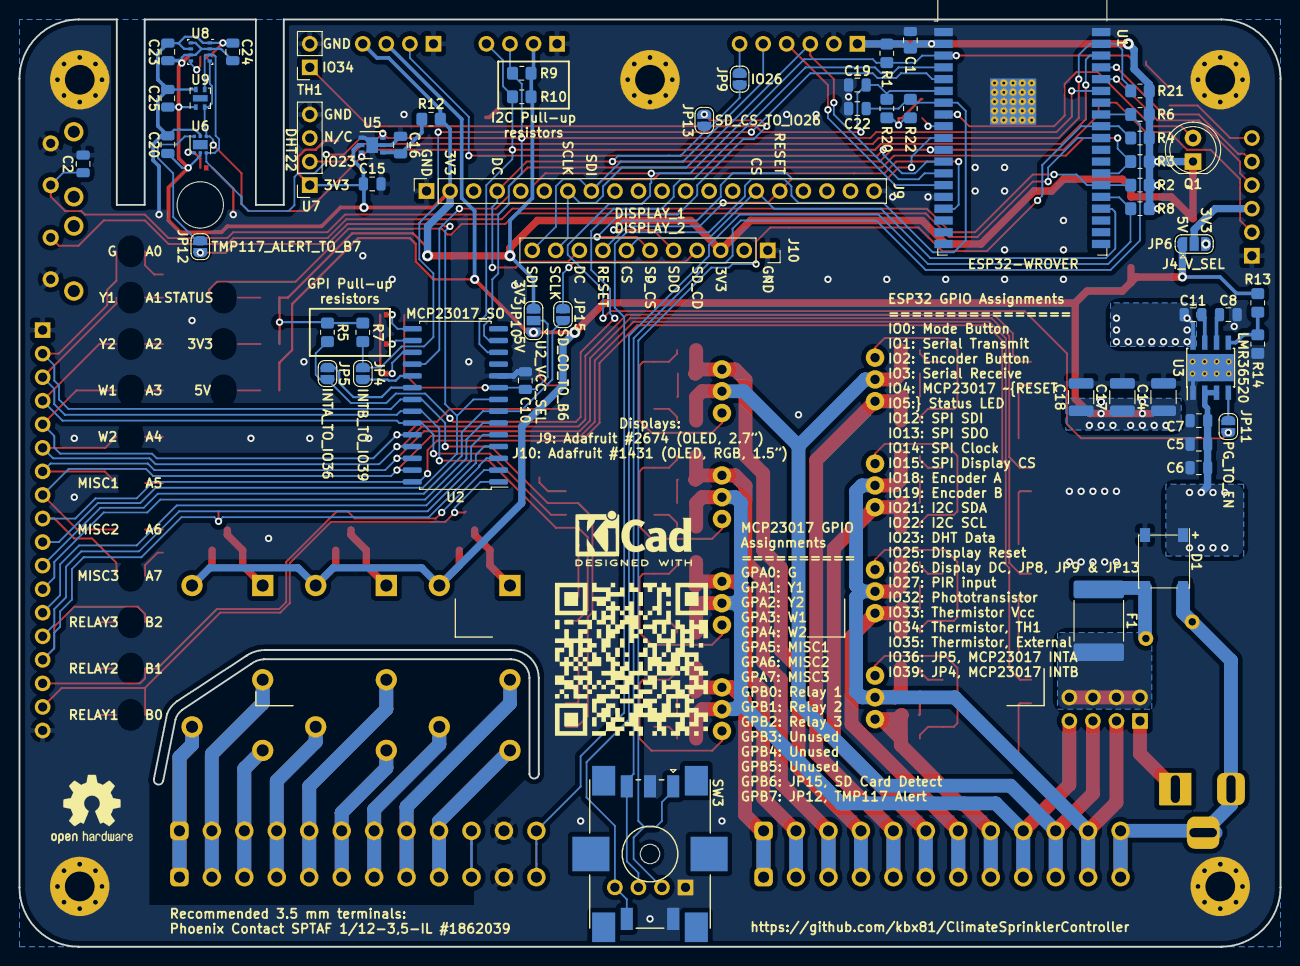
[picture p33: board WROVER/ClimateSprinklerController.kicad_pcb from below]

Board: 2 copper layers, 136.0 x 100.0 mm, 190 parts (61 on the bottom side), 141 nets.

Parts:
C1: 10 uF; C_0805_2012Metric
C2, C4, C10, C11, C19, C20, C21, C22, C23, C24, C25: 100 nF; C_0805_2012Metric
C3: 470 uF; CP_Elec_16x17.5
C5, C6: 4.7 uF; C_0805_2012Metric
C7: 220 nF; C_0805_2012Metric
C8, C15, C16: 1 uF; C_0805_2012Metric
C9, C12: 10 uF; CP_Elec_5x5.8
C13: 220 uF; CP_Elec_8x10
C14, C17, C18: 47 uF; C_1210_3225Metric
C26, C27, C28, C29, C30, C31, C32, C33: .01 uF; C_0805_2012Metric
D1: N/A; Diode_Bridge_Bourns_CD-MBL2xxS
D2: 3V3; LED_1206_3216Metric_ReverseMount_Hole1.8x2.4mm
D3: STATUS; LED_1206_3216Metric_ReverseMount_Hole1.8x2.4mm
D4: 5V; LED_1206_3216Metric_ReverseMount_Hole1.8x2.4mm
D5, D7, D9: N/A; D_SOD-123
D6: RELAY1; LED_1206_3216Metric_ReverseMount_Hole1.8x2.4mm
D8: RELAY2; LED_1206_3216Metric_ReverseMount_Hole1.8x2.4mm
D10: RELAY3; LED_1206_3216Metric_ReverseMount_Hole1.8x2.4mm
D11: G; LED_1206_3216Metric_ReverseMount_Hole1.8x2.4mm
D12: Y1; LED_1206_3216Metric_ReverseMount_Hole1.8x2.4mm
D13: Y2; LED_1206_3216Metric_ReverseMount_Hole1.8x2.4mm
D14: W1; LED_1206_3216Metric_ReverseMount_Hole1.8x2.4mm
D15: W2; LED_1206_3216Metric_ReverseMount_Hole1.8x2.4mm
D16: MISC1; LED_1206_3216Metric_ReverseMount_Hole1.8x2.4mm
D17: MISC2; LED_1206_3216Metric_ReverseMount_Hole1.8x2.4mm
D18: MISC3; LED_1206_3216Metric_ReverseMount_Hole1.8x2.4mm
F1: 300 mA; Fuse_2920_7451Metric
H1, H2, H3, H4, H5: MountingHole_Pad; MountingHole_3.2mm_M3_Pad_Via
H6: MountingHole; MountingHole_5mm
J1: 7.5 TO 40 V; BarrelJack_Horizontal
J2: POWER SEL; PinHeader_2x04_P2.54mm_Vertical
J3: EXT_ENC; PinSocket_1x04_P2.54mm_Vertical
J4: SERIAL; PinSocket_1x06_P2.54mm_Vertical
J5: SPI; PinSocket_1x06_P2.54mm_Vertical
J6: I2C; PinSocket_1x04_P2.54mm_Vertical
J7: PIR; PinSocket_1x04_P2.54mm_Vertical
J8: IO_EXP; PinSocket_1x18_P2.54mm_Vertical
J9: DISPLAY_1; PinSocket_1x20_P2.54mm_Vertical
J10: DISPLAY_2; PinSocket_1x11_P2.54mm_Vertical
J11: HVAC; PhoenixContact_SPTAF_1_12-3.5-IL_1x12_P3.50mm_Vertical
J12: RELAY; PhoenixContact_SPTAF_1_12-3.5-IL_1x12_P3.50mm_Vertical
JP1: MCP23017_A0; SolderJumper-3_P1.3mm_Bridged12_RoundedPad1.0x1.5mm
JP2: MCP23017_A1; SolderJumper-3_P1.3mm_Bridged12_RoundedPad1.0x1.5mm
JP3: MCP23017_A2; SolderJumper-3_P1.3mm_Bridged12_RoundedPad1.0x1.5mm
JP4: INTB_TO_IO39; SolderJumper-2_P1.3mm_Open_RoundedPad1.0x1.5mm
JP5: INTA_TO_IO36; SolderJumper-2_P1.3mm_Open_RoundedPad1.0x1.5mm
JP6: J4_V_SEL; SolderJumper-3_P1.3mm_Open_RoundedPad1.0x1.5mm
JP7: EN; SolderJumper-2_P1.3mm_Open_RoundedPad1.0x1.5mm
JP8, JP9: IO26; SolderJumper-2_P1.3mm_Open_RoundedPad1.0x1.5mm
JP10: U2_VCC_SEL; SolderJumper-3_P1.3mm_Open_RoundedPad1.0x1.5mm
JP11: PG_TO_EN; SolderJumper-2_P1.3mm_Open_RoundedPad1.0x1.5mm
JP12: TMP117_ALERT_TO_B7; SolderJumper-2_P1.3mm_Open_RoundedPad1.0x1.5mm
JP13: SD_CS_TO_IO26; SolderJumper-2_P1.3mm_Open_RoundedPad1.0x1.5mm
JP14: TMP117_A0; SolderJumper-3_P1.3mm_Bridged12_RoundedPad1.0x1.5mm
JP15: SD_CD_TO_B6; SolderJumper-2_P1.3mm_Open_RoundedPad1.0x1.5mm
JP16: BME280_A0; SolderJumper-3_P1.3mm_Bridged12_RoundedPad1.0x1.5mm
K1, K2, K3: G5Q-1-DC5; Relay_SPDT_Omron-G5Q-1
L1: 15 uH; L_Wuerth_WE-PD-Typ-LS
Q1: TEPT5700; LED_D5.0mm_Clear
Q2, Q3, Q4: 2N7002; SOT-23
Q5, Q6, Q7, Q8, Q9, Q10, Q11, Q12: 2N6073B; TO-225-3_Vertical
QR*****: ClimateSprinklerControllerQR
R1, R2, R3, R4, R5, R6, R7, R8, R16, R20, R21, R22, R26: 10K; R_0805_2012Metric_Pad1.20x1.40mm_HandSolder
R9, R10: 3K3; R_0805_2012Metric_Pad1.20x1.40mm_HandSolder
R11, R13: 100K; R_0805_2012Metric_Pad1.20x1.40mm_HandSolder
R12: 4.7; R_0805_2012Metric_Pad1.20x1.40mm_HandSolder
R14: 24.9K; R_0805_2012Metric_Pad1.20x1.40mm_HandSolder
R15: 1K6; R_0805_2012Metric_Pad1.20x1.40mm_HandSolder
R17: 5K; R_0805_2012Metric_Pad1.20x1.40mm_HandSolder
R18: 120; R_0805_2012Metric_Pad1.20x1.40mm_HandSolder
R19: 8K2; R_0805_2012Metric_Pad1.20x1.40mm_HandSolder
R23, R24, R25: 560; R_0805_2012Metric_Pad1.20x1.40mm_HandSolder
R27, R28, R31, R32, R33: 1K5; R_0805_2012Metric_Pad1.20x1.40mm_HandSolder
R29, R30: 2K7; R_0805_2012Metric_Pad1.20x1.40mm_HandSolder
R34, R35, R36, R37, R38, R39, R40, R41: 270; R_0805_2012Metric_Pad1.20x1.40mm_HandSolder
R42, R43, R44, R45, R46, R47, R48, R49: 180; R_0805_2012Metric_Pad1.20x1.40mm_HandSolder
R50, R51, R52, R53, R54, R55, R56, R57: 820; R_0805_2012Metric_Pad1.20x1.40mm_HandSolder
R58, R59, R60, R61, R62, R63, R64, R65: 39; R_0805_2012Metric_Pad1.20x1.40mm_HandSolder
RV1: N/A; RV_Disc_D7mm_W4mm_P5mm
SW1: RESET; SW_Tactile_SPST_Angled_PTS645Vx58-2LFS
SW2: MODE; SW_Tactile_SPST_Angled_PTS645Vx58-2LFS
SW3: PEC11S-929K-S0015; RotaryEncoder_Bourns_PEC11S-Switch_Vertical_H9.5mm
TH1: 10K; PinSocket_1x02_P2.54mm_Vertical
U1: ESP32-WROVER
U2: MCP23017_SO; SOIC-28W_7.5x17.9mm_P1.27mm
U3: LMR36520; Texas_HSOP-8-1EP_3.9x4.9mm_P1.27mm_ThermalVias
U4: LD1086DT33TR; TO-252-2
U5: SGP40-Sensor_Air_Quality; DFN-6-1EP_2.44x2.44mm_P0.8mm_EP1.25x1.7mm
U6: TMP117; WSON-6-1EP_2x2mm_P0.65mm_EP1x1.6mm
U7: DHT22; PinSocket_1x04_P2.54mm_Vertical
U8: BME280; Bosch_LGA-8_2.5x2.5mm_P0.65mm_ClockwisePinNumbering
U9: SHTC3; AMS_QFN-4-1EP_2x2mm_P0.95mm_EP0.7x1.6mm
U10, U11, U12, U13, U14, U15, U16, U17: MOC3043; SMDIP-6_W9.53mm

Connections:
+3V3: C1.2, C12.1, C13.1, C15.2, C20.1, C21.1, C23.1, C24.1, C25.1, J5.1, J6.2, J7.4, J9.2, J10.3, JP6.3, JP10.3, JP14.3, JP16.3, Q1.1, R1.2, R2.2, R3.1, R4.1, R5.1, R6.1, R7.1, R8.1, R9.1, R10.1, R12.1, R15.1, R18.1, R21.2, U1.2, U4.2, U5.5, U6.5, U7.1, U8.2, U8.6, U8.8, U9.1
+5V: C9.1, C14.1, C17.1, C18.1, D5.1, D7.1, D9.1, J7.3, JP6.1, JP10.1, K1.5, K2.5, K3.5, L1.2, R13.1, R19.2, U4.3
+VDC: C3.1, C5.1, C6.1, C7.1, D1.1, U3.2, U3.3
/C_TERM: D1.2, J1.2, J1.3, J11.12, RV1.2
/DHT_DATA: R21.1, U1.37, U7.2
/DISP_CS: J9.15, J10.7, U1.23
/DISP_D0_SCLK: J5.3, J9.7, J10.10, U1.13
/DISP_D1_DIN: J5.5, J9.8, J10.11, U1.16
/DISP_DC: J9.4, J10.9, JP8.2, JP9.2, JP13.2, U1.11
/DISP_RESET: J9.16, J10.8, U1.10
/ENCODER_A: J3.2, R4.2, SW3.A, U1.30
/ENCODER_B: J3.3, R6.2, SW3.B, U1.31
/ENCODER_SW: J3.4, R8.2, SW3.S2, U1.24
/ESP_MISO: J5.4, J10.5, U1.14
/ESP_RXD: J4.4, U1.34
/ESP_TXD: J4.5, U1.35
/G_TERM: C26.2, J11.1, Q5.1, R50.2
/I2C_SCL: J6.4, R10.2, U1.36, U2.12, U5.6, U6.1, U8.4, U9.2
/I2C_SDA: J6.3, R9.2, U1.33, U2.13, U5.3, U6.6, U8.3, U9.3
/MCP23017_A0: JP1.2, U2.15
/MCP23017_A1: JP2.2, U2.16
/MCP23017_A2: JP3.2, U2.17
/MCP23017_GPA0: D11.2, J8.2, U2.21, U10.1
/MCP23017_GPA1: D12.2, J8.3, U2.22, U11.1
/MCP23017_GPA2: D13.2, J8.4, U2.23, U12.1
/MCP23017_GPA3: D14.2, J8.5, U2.24, U13.1
/MCP23017_GPA4: D15.2, J8.6, U2.25, U14.1
/MCP23017_GPA5: D16.2, J8.7, U2.26, U15.1
/MCP23017_GPA6: D17.2, J8.8, U2.27, U16.1
/MCP23017_GPA7: D18.2, J8.9, U2.28, U17.1
/MCP23017_GPB0: D6.2, J8.17, Q2.1, U2.1
/MCP23017_GPB1: D8.2, J8.16, Q3.1, U2.2
/MCP23017_GPB2: D10.2, J8.15, Q4.1, U2.3
/MCP23017_GPB3: J8.14, U2.4
/MCP23017_GPB4: J8.13, U2.5
/MCP23017_GPB5: J8.12, U2.6
/MCP23017_GPB6: J8.11, JP15.2, U2.7
/MCP23017_GPB7: J8.10, JP12.2, U2.8
/MCP23017_INTA: JP5.2, R5.2, U1.4
/MCP23017_INTB: JP4.2, R7.2, U1.5
/MCP23017_~RESET: R3.2, U1.26, U2.18
/MISC1_TERM: C31.2, J11.6, Q10.1, R55.2
/MISC2_TERM: C32.2, J11.7, Q11.1, R56.2
/MISC3_TERM: C33.2, J11.8, Q12.1, R57.2
/MODE: R2.1, SW2.1, U1.25
/PHOTO: Q1.2, R11.2, U1.8
/PIR: J7.2, U1.12
/RC_TERM: J2.7, J11.9, Q5.2, Q6.2, Q7.2, R42.1, R43.1, R44.1, R58.1, R59.1, R60.1
/RELAY_1_COM_TERM: J12.8, K1.2
/RELAY_1_NC_TERM: J12.7, K1.4
/RELAY_1_NO_TERM: J12.9, K1.3
/RELAY_2_COM_TERM: J12.5, K2.2
/RELAY_2_NC_TERM: J12.4, K2.4
/RELAY_2_NO_TERM: J12.6, K2.3
/RELAY_3_COM_TERM: J12.2, K3.2
/RELAY_3_NC_TERM: J12.1, K3.4
/RELAY_3_NO_TERM: J12.3, K3.3
/RH_TERM: J2.5, J11.10, Q8.2, Q9.2, R45.1, R46.1, R61.1, R62.1
/RMISC_TERM: J2.3, J11.11, Q10.2, Q11.2, Q12.2, R47.1, R48.1, R49.1, R63.1, R64.1, R65.1
/SD_CD: J10.4, JP15.1
/SD_CS: J10.6, JP13.1
/STATUS: D3.1, U1.29
/THERMISTOR_1V1: R16.1, R17.2, R20.2, R22.1
/THERMISTOR_EXT: C22.1, J12.12, R22.2, U1.7
/THERMISTOR_INT: C19.1, R20.1, TH1.1, U1.6
/THERMISTOR_VCC: R16.2, U1.9
/TMP117_ALERT: JP12.1, U6.3
/W1_TERM: C29.2, J11.4, Q8.1, R53.2
/W2_TERM: C30.2, J11.5, Q9.1, R54.2
/Y1_TERM: C27.2, J11.2, Q6.1, R51.2
/Y2_TERM: C28.2, J11.3, Q7.1, R52.2
/~ESP_RESET: C2.1, JP7.2, JP11.1, R1.1, SW1.2, U1.3
GND: C1.1, C2.2, C3.2, C5.2, C6.2, C7.2, C8.2, C9.2, C10.2, C12.2, C13.2, C14.2, C15.1, C16.1, C17.2, C18.2, C19.2, C20.2, C21.2, C22.2, C23.2, C24.2, C25.2, D1.4, D2.1, D4.1, H1.1, H2.1, H3.1, H4.1, H5.1, J3.1, J4.1, J5.2, J6.1, J7.1, J8.1, J8.18, J9.1, J9.20, J10.1, J12.11, JP1.1, JP2.1, JP3.1, JP14.1, JP16.1, Q2.2, Q3.2, Q4.2, R11.1, R14.2, R17.1, R23.1, R24.1, R25.1, R26.2, R27.2, R28.2, R29.2, R30.2, R31.2, R32.2, R33.2, R34.2, R35.2, R36.2, R37.2, R38.2, R39.2, R40.2, R41.2, SW1.1, SW2.2, SW3.C, SW3.S1, TH1.2, U1.1, U1.15, U1.38, U1.39, U2.10, U3.1, U3.9, U4.1, U5.2, U5.4, U5.7, U6.2, U7.4, U8.1, U8.7, U9.4
unnamed: C4.1, JP7.1
unnamed: C4.2, J4.6
unnamed: C8.1, U3.6
unnamed: C10.1, JP1.3, JP2.3, JP3.3, JP10.2, U2.9
unnamed: C11.1, U3.7
unnamed: C11.2, L1.1, U3.8
unnamed: C16.2, R12.2, U5.1
unnamed: C26.1, R58.2
unnamed: C27.1, R59.2
unnamed: C28.1, R60.2
unnamed: C29.1, R61.2
unnamed: C30.1, R62.2
unnamed: C31.1, R63.2
unnamed: C32.1, R64.2
unnamed: C33.1, R65.2
unnamed: D1.3, F1.2, RV1.1
unnamed: D2.2, R15.2
unnamed: D3.2, R18.2
unnamed: D4.2, R19.1
unnamed: D5.2, K1.1, Q2.3
unnamed: D6.1, R23.2
unnamed: D7.2, K2.1, Q3.3
unnamed: D8.1, R24.2
unnamed: D9.2, K3.1, Q4.3
unnamed: D10.1, R25.2
unnamed: D11.1, R26.1
unnamed: D12.1, R27.1
unnamed: D13.1, R28.1
unnamed: D14.1, R29.1
unnamed: D15.1, R30.1
unnamed: D16.1, R31.1
unnamed: D17.1, R32.1
unnamed: D18.1, R33.1
unnamed: F1.1, J2.2, J2.4, J2.6, J2.8
unnamed: J1.1, J2.1
unnamed: J4.2, JP8.1
unnamed: J4.3, JP6.2
unnamed: J5.6, JP9.1
unnamed: JP4.1, U2.19
unnamed: JP5.1, U2.20
unnamed: JP11.2, U3.4
unnamed: JP14.2, U6.4
unnamed: JP16.2, U8.5
unnamed: Q5.3, R50.1, U10.4
unnamed: Q6.3, R51.1, U11.4
unnamed: Q7.3, R52.1, U12.4
unnamed: Q8.3, R53.1, U13.4
unnamed: Q9.3, R54.1, U14.4
unnamed: Q10.3, R55.1, U15.4
unnamed: Q11.3, R56.1, U16.4
unnamed: Q12.3, R57.1, U17.4
unnamed: R13.2, R14.1, U3.5
unnamed: R34.1, U10.2
unnamed: R35.1, U11.2
unnamed: R36.1, U12.2
unnamed: R37.1, U13.2
unnamed: R38.1, U14.2
unnamed: R39.1, U15.2
unnamed: R40.1, U16.2
unnamed: R41.1, U17.2
unnamed: R42.2, U10.6
unnamed: R43.2, U11.6
unnamed: R44.2, U12.6
unnamed: R45.2, U13.6
unnamed: R46.2, U14.6
unnamed: R47.2, U15.6
unnamed: R48.2, U16.6
unnamed: R49.2, U17.6

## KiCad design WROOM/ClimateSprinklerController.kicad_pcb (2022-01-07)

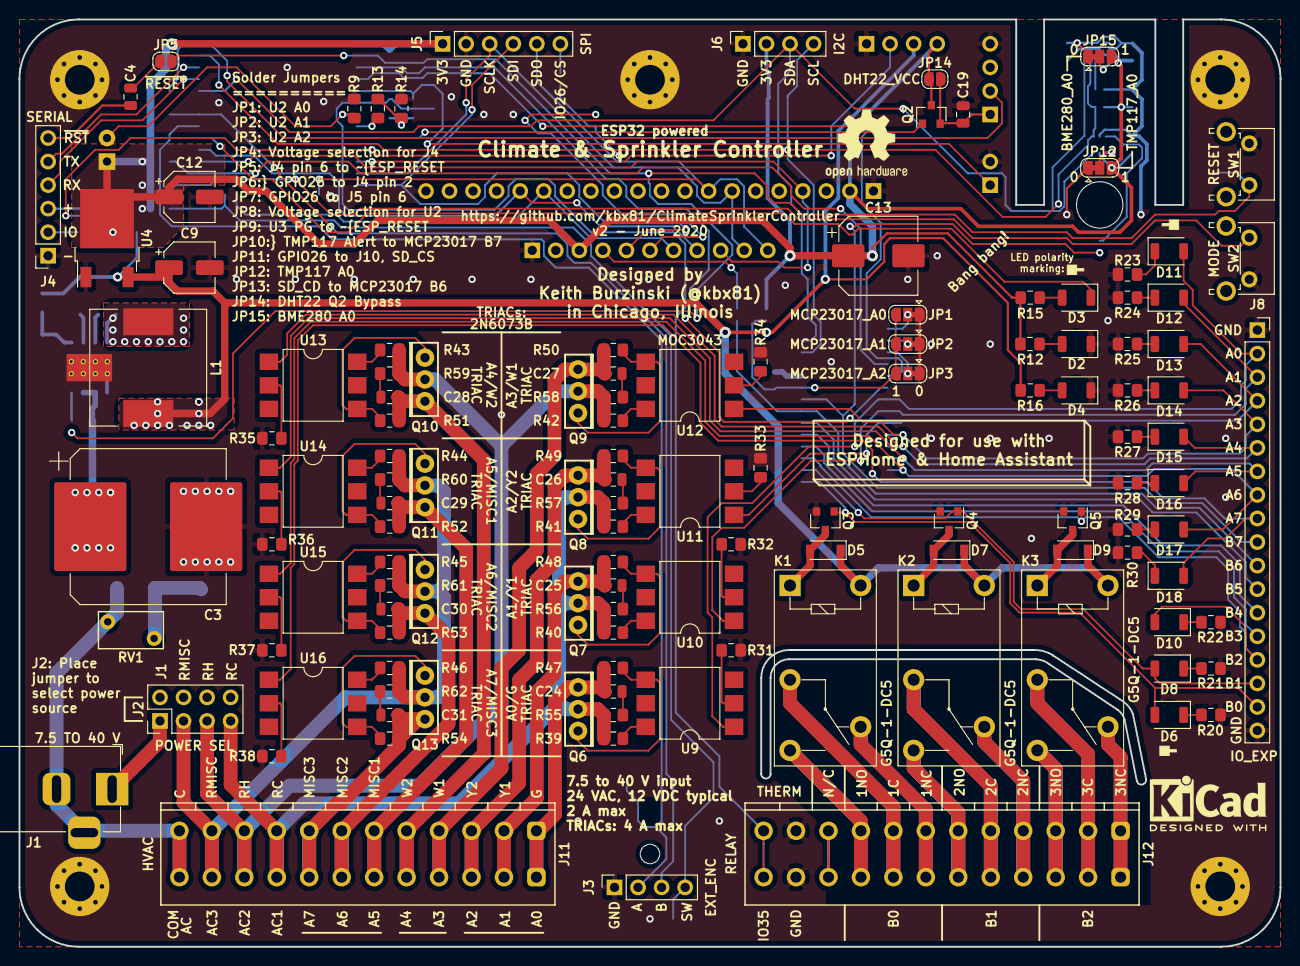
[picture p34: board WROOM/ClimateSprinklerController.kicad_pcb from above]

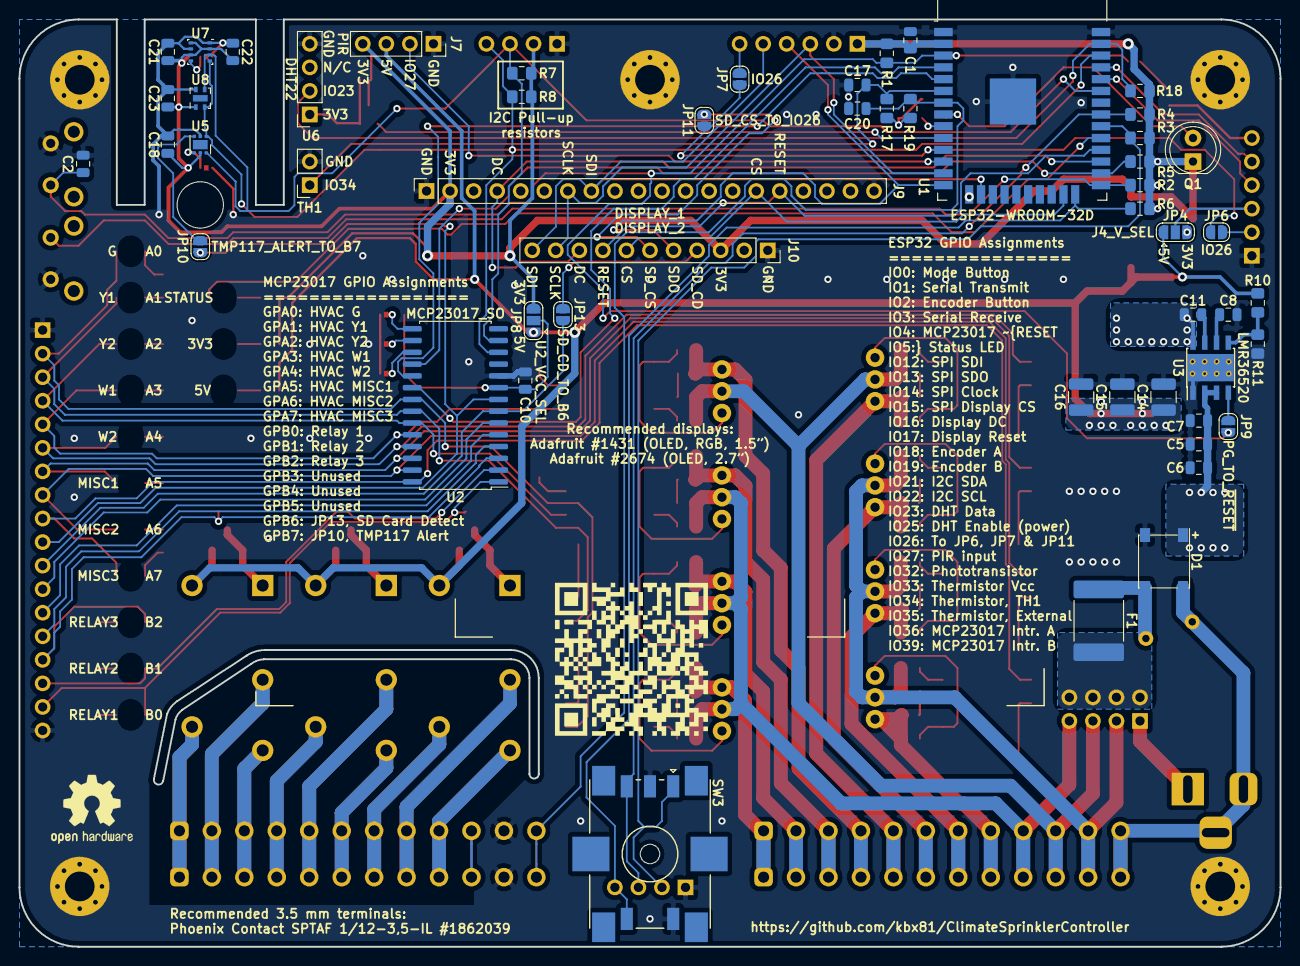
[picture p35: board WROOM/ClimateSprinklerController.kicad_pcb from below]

Board: 2 copper layers, 136.0 x 100.0 mm, 184 parts (55 on the bottom side), 141 nets.

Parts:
C1: 10 uF; C_0805_2012Metric
C2, C4, C10, C11, C17, C18, C19, C20, C21, C22, C23: 100 nF; C_0805_2012Metric
C3: 470 uF; CP_Elec_16x17.5
C5, C6: 4.7 uF; C_0805_2012Metric
C7: 220 nF; C_0805_2012Metric
C8: 1 uF; C_0805_2012Metric
C9, C12: 10 uF; CP_Elec_5x5.8
C13: 220 uF; CP_Elec_8x10
C14, C15, C16: 47 uF; C_1210_3225Metric
C24, C25, C26, C27, C28, C29, C30, C31: .01 uF; C_0805_2012Metric
D1: N/A; Diode_Bridge_Bourns_CD-MBL2xxS
D2: 3V3; LED_1206_3216Metric_ReverseMount_Hole1.8x2.4mm
D3: STATUS; LED_1206_3216Metric_ReverseMount_Hole1.8x2.4mm
D4: 5V; LED_1206_3216Metric_ReverseMount_Hole1.8x2.4mm
D5, D7, D9: N/A; D_SOD-123
D6: RELAY1; LED_1206_3216Metric_ReverseMount_Hole1.8x2.4mm
D8: RELAY2; LED_1206_3216Metric_ReverseMount_Hole1.8x2.4mm
D10: RELAY3; LED_1206_3216Metric_ReverseMount_Hole1.8x2.4mm
D11: G; LED_1206_3216Metric_ReverseMount_Hole1.8x2.4mm
D12: Y1; LED_1206_3216Metric_ReverseMount_Hole1.8x2.4mm
D13: Y2; LED_1206_3216Metric_ReverseMount_Hole1.8x2.4mm
D14: W1; LED_1206_3216Metric_ReverseMount_Hole1.8x2.4mm
D15: W2; LED_1206_3216Metric_ReverseMount_Hole1.8x2.4mm
D16: MISC1; LED_1206_3216Metric_ReverseMount_Hole1.8x2.4mm
D17: MISC2; LED_1206_3216Metric_ReverseMount_Hole1.8x2.4mm
D18: MISC3; LED_1206_3216Metric_ReverseMount_Hole1.8x2.4mm
F1: 300 mA; Fuse_2920_7451Metric
H1, H2, H3, H4, H5: MountingHole_Pad; MountingHole_3.2mm_M3_Pad_Via
H6: MountingHole; MountingHole_5mm
J1: 7.5 TO 40 V; BarrelJack_Horizontal
J2: POWER SEL; PinHeader_2x04_P2.54mm_Vertical
J3: EXT_ENC; PinSocket_1x04_P2.54mm_Vertical
J4: SERIAL; PinSocket_1x06_P2.54mm_Vertical
J5: SPI; PinSocket_1x06_P2.54mm_Vertical
J6: I2C; PinSocket_1x04_P2.54mm_Vertical
J7: PIR; PinSocket_1x04_P2.54mm_Vertical
J8: IO_EXP; PinSocket_1x18_P2.54mm_Vertical
J9: DISPLAY_1; PinSocket_1x20_P2.54mm_Vertical
J10: DISPLAY_2; PinSocket_1x11_P2.54mm_Vertical
J11: HVAC; PhoenixContact_SPTAF_1_12-3.5-IL_1x12_P3.50mm_Vertical
J12: RELAY; PhoenixContact_SPTAF_1_12-3.5-IL_1x12_P3.50mm_Vertical
JP1: MCP23017_A0; SolderJumper-3_P1.3mm_Bridged12_RoundedPad1.0x1.5mm
JP2: MCP23017_A1; SolderJumper-3_P1.3mm_Bridged12_RoundedPad1.0x1.5mm
JP3: MCP23017_A2; SolderJumper-3_P1.3mm_Bridged12_RoundedPad1.0x1.5mm
JP4: J4_V_SEL; SolderJumper-3_P1.3mm_Open_RoundedPad1.0x1.5mm
JP5: ~RESET; SolderJumper-2_P1.3mm_Open_RoundedPad1.0x1.5mm
JP6, JP7: IO26; SolderJumper-2_P1.3mm_Open_RoundedPad1.0x1.5mm
JP8: U2_VCC_SEL; SolderJumper-3_P1.3mm_Open_RoundedPad1.0x1.5mm
JP9: PG_TO_~RESET; SolderJumper-2_P1.3mm_Open_RoundedPad1.0x1.5mm
JP10: TMP117_ALERT_TO_B7; SolderJumper-2_P1.3mm_Open_RoundedPad1.0x1.5mm
JP11: SD_CS_TO_IO26; SolderJumper-2_P1.3mm_Open_RoundedPad1.0x1.5mm
JP12: TMP117_A0; SolderJumper-3_P1.3mm_Bridged12_RoundedPad1.0x1.5mm
JP13: SD_CD_TO_B6; SolderJumper-2_P1.3mm_Open_RoundedPad1.0x1.5mm
JP14: DHT22_VCC; SolderJumper-2_P1.3mm_Open_RoundedPad1.0x1.5mm
JP15: BME280_A0; SolderJumper-3_P1.3mm_Bridged12_RoundedPad1.0x1.5mm
K1, K2, K3: G5Q-1-DC5; Relay_SPDT_Omron-G5Q-1
L1: 15 uH; L_Wuerth_WE-PD-Typ-LS
Q1: TEPT5700; LED_D5.0mm_Clear
Q2, Q3, Q4, Q5: 2N7002; SOT-23
Q6, Q7, Q8, Q9, Q10, Q11, Q12, Q13: 2N6073B; TO-225-3_Vertical
QR*****: ClimateSprinklerControllerQR
R1, R2, R3, R4, R5, R6, R13, R17, R18, R19, R23: 10K; R_0805_2012Metric_Pad1.15x1.40mm_HandSolder
R7, R8: 3K3; R_0805_2012Metric_Pad1.15x1.40mm_HandSolder
R9, R10: 100K; R_0805_2012Metric_Pad1.15x1.40mm_HandSolder
R11: 24.9K; R_0805_2012Metric_Pad1.15x1.40mm_HandSolder
R12: 1K6; R_0805_2012Metric_Pad1.15x1.40mm_HandSolder
R14: 5K; R_0805_2012Metric_Pad1.15x1.40mm_HandSolder
R15: 120; R_0805_2012Metric_Pad1.15x1.40mm_HandSolder
R16: 8K2; R_0805_2012Metric_Pad1.15x1.40mm_HandSolder
R20, R21, R22: 560; R_0805_2012Metric_Pad1.15x1.40mm_HandSolder
R24, R25, R28, R29, R30: 1K5; R_0805_2012Metric_Pad1.15x1.40mm_HandSolder
R26, R27: 2K7; R_0805_2012Metric_Pad1.15x1.40mm_HandSolder
R31, R32, R33, R34, R35, R36, R37, R38: 270; R_0805_2012Metric_Pad1.15x1.40mm_HandSolder
R39, R40, R41, R42, R43, R44, R45, R46: 180; R_0805_2012Metric_Pad1.15x1.40mm_HandSolder
R47, R48, R49, R50, R51, R52, R53, R54: 820; R_0805_2012Metric_Pad1.15x1.40mm_HandSolder
R55, R56, R57, R58, R59, R60, R61, R62: 39; R_0805_2012Metric_Pad1.15x1.40mm_HandSolder
RV1: N/A; RV_Disc_D7mm_W4mm_P5mm
SW1: RESET; SW_Tactile_SPST_Angled_PTS645Vx58-2LFS
SW2: MODE; SW_Tactile_SPST_Angled_PTS645Vx58-2LFS
SW3: PEC11S-929K-S0015; RotaryEncoder_Bourns_PEC11S-Switch_Vertical_H9.5mm
TH1: 10K; PinSocket_1x02_P2.54mm_Vertical
U1: ESP32-WROOM-32D; ESP32-WROOM-32
U2: MCP23017_SO; SOIC-28W_7.5x17.9mm_P1.27mm
U3: LMR36520; Texas_HSOP-8-1EP_3.9x4.9mm_P1.27mm_ThermalVias
U4: LD1086DT33TR; TO-252-2
U5: TMP117; WSON-6-1EP_2x2mm_P0.65mm_EP1x1.6mm
U6: DHT22; PinSocket_1x04_P2.54mm_Vertical
U7: BME280; Bosch_LGA-8_2.5x2.5mm_P0.65mm_ClockwisePinNumbering
U8: SHTC3; AMS_QFN-4-1EP_2x2mm_P0.95mm_EP0.7x1.6mm
U9, U10, U11, U12, U13, U14, U15, U16: MOC3043; SMDIP-6_W9.53mm

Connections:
+3V3: C1.2, C12.1, C13.1, C18.1, C21.1, C22.1, C23.1, J5.1, J6.2, J7.4, J9.2, J10.3, JP4.3, JP8.3, JP12.3, JP14.1, JP15.3, Q1.1, Q2.3, R1.2, R2.2, R3.1, R4.1, R5.1, R6.1, R7.1, R8.1, R12.1, R15.1, R18.2, U1.2, U4.2, U5.5, U7.2, U7.6, U7.8, U8.1
+5V: C9.1, C14.1, C15.1, C16.1, D5.1, D7.1, D9.1, J7.3, JP4.1, JP8.1, K1.5, K2.5, K3.5, L1.2, R10.1, R16.2, U4.3
+VDC: C3.1, C5.1, C6.1, C7.1, D1.1, U3.2, U3.3
/C_TERM: D1.2, J1.2, J1.3, J11.12, RV1.2
/DHT_DATA: R18.1, U1.37, U6.2
/DHT_EN: Q2.1, U1.10
/DISP_CS: J9.15, J10.7, U1.23
/DISP_D0_SCLK: J5.3, J9.7, J10.10, U1.13
/DISP_D1_DIN: J5.5, J9.8, J10.11, U1.16
/DISP_DC: J9.4, J10.9, U1.27
/DISP_RESET: J9.16, J10.8, U1.28
/ENCODER_A: J3.2, R3.2, SW3.A, U1.30
/ENCODER_B: J3.3, R4.2, SW3.B, U1.31
/ENCODER_SW: J3.4, R6.2, SW3.S2, U1.24
/ESP_GPIO26: JP6.2, JP7.2, JP11.2, U1.11
/ESP_MISO: J5.4, J10.5, U1.14
/ESP_RXD: J4.4, U1.34
/ESP_TXD: J4.5, U1.35
/G_TERM: C24.2, J11.1, Q6.1, R47.2
/I2C_SCL: J6.4, R8.2, U1.36, U2.12, U5.1, U7.4, U8.2
/I2C_SDA: J6.3, R7.2, U1.33, U2.13, U5.6, U7.3, U8.3
/MCP23017_A0: JP1.2, U2.15
/MCP23017_A1: JP2.2, U2.16
/MCP23017_A2: JP3.2, U2.17
/MCP23017_GPA0: D11.2, J8.2, U2.21, U9.1
/MCP23017_GPA1: D12.2, J8.3, U2.22, U10.1
/MCP23017_GPA2: D13.2, J8.4, U2.23, U11.1
/MCP23017_GPA3: D14.2, J8.5, U2.24, U12.1
/MCP23017_GPA4: D15.2, J8.6, U2.25, U13.1
/MCP23017_GPA5: D16.2, J8.7, U2.26, U14.1
/MCP23017_GPA6: D17.2, J8.8, U2.27, U15.1
/MCP23017_GPA7: D18.2, J8.9, U2.28, U16.1
/MCP23017_GPB0: D6.2, J8.17, Q3.1, U2.1
/MCP23017_GPB1: D8.2, J8.16, Q4.1, U2.2
/MCP23017_GPB2: D10.2, J8.15, Q5.1, U2.3
/MCP23017_GPB3: J8.14, U2.4
/MCP23017_GPB4: J8.13, U2.5
/MCP23017_GPB5: J8.12, U2.6
/MCP23017_GPB6: J8.11, JP13.2, U2.7
/MCP23017_GPB7: J8.10, JP10.2, U2.8
/MCP23017_INTA: U1.4, U2.20
/MCP23017_INTB: U1.5, U2.19
/MCP23017_~RESET: R5.2, U1.26, U2.18
/MISC1_TERM: C29.2, J11.6, Q11.1, R52.2
/MISC2_TERM: C30.2, J11.7, Q12.1, R53.2
/MISC3_TERM: C31.2, J11.8, Q13.1, R54.2
/MODE: R2.1, SW2.1, U1.25
/PHOTO: Q1.2, R9.2, U1.8
/PIR: J7.2, U1.12
/RC_TERM: J2.7, J11.9, Q6.2, Q7.2, Q8.2, R39.1, R40.1, R41.1, R55.1, R56.1, R57.1
/RELAY_1_COM_TERM: J12.8, K1.2
/RELAY_1_NC_TERM: J12.7, K1.4
/RELAY_1_NO_TERM: J12.9, K1.3
/RELAY_2_COM_TERM: J12.5, K2.2
/RELAY_2_NC_TERM: J12.4, K2.4
/RELAY_2_NO_TERM: J12.6, K2.3
/RELAY_3_COM_TERM: J12.2, K3.2
/RELAY_3_NC_TERM: J12.1, K3.4
/RELAY_3_NO_TERM: J12.3, K3.3
/RH_TERM: J2.5, J11.10, Q9.2, Q10.2, R42.1, R43.1, R58.1, R59.1
/RMISC_TERM: J2.3, J11.11, Q11.2, Q12.2, Q13.2, R44.1, R45.1, R46.1, R60.1, R61.1, R62.1
/SD_CD: J10.4, JP13.1
/SD_CS: J10.6, JP11.1
/STATUS: D3.1, U1.29
/THERMISTOR_1V1: R13.1, R14.2, R17.2, R19.1
/THERMISTOR_EXT: C20.1, J12.12, R19.2, U1.7
/THERMISTOR_INT: C17.1, R17.1, TH1.1, U1.6
/THERMISTOR_VCC: R13.2, U1.9
/TMP117_ALERT: JP10.1, U5.3
/W1_TERM: C27.2, J11.4, Q9.1, R50.2
/W2_TERM: C28.2, J11.5, Q10.1, R51.2
/Y1_TERM: C25.2, J11.2, Q7.1, R48.2
/Y2_TERM: C26.2, J11.3, Q8.1, R49.2
/~ESP_RESET: C2.1, JP5.2, JP9.1, R1.1, SW1.2, U1.3
GND: C1.1, C2.2, C3.2, C5.2, C6.2, C7.2, C8.2, C9.2, C10.2, C12.2, C13.2, C14.2, C15.2, C16.2, C17.2, C18.2, C19.2, C20.2, C21.2, C22.2, C23.2, D1.4, D2.1, D4.1, H1.1, H2.1, H3.1, H4.1, H5.1, J3.1, J4.1, J5.2, J6.1, J7.1, J8.1, J8.18, J9.1, J9.20, J10.1, J12.11, JP1.1, JP2.1, JP3.1, JP12.1, JP15.1, Q3.2, Q4.2, Q5.2, R9.1, R11.2, R14.1, R20.1, R21.1, R22.1, R23.2, R24.2, R25.2, R26.2, R27.2, R28.2, R29.2, R30.2, R31.2, R32.2, R33.2, R34.2, R35.2, R36.2, R37.2, R38.2, SW1.1, SW2.2, SW3.C, SW3.S1, TH1.2, U1.1, U1.15, U1.38, U1.39, U2.10, U3.1, U3.9, U4.1, U5.2, U6.4, U7.1, U7.7, U8.4
unnamed: C4.1, JP5.1
unnamed: C4.2, J4.6
unnamed: C8.1, U3.6
unnamed: C10.1, JP1.3, JP2.3, JP3.3, JP8.2, U2.9
unnamed: C11.1, U3.7
unnamed: C11.2, L1.1, U3.8
unnamed: C19.1, JP14.2, Q2.2, U6.1
unnamed: C24.1, R55.2
unnamed: C25.1, R56.2
unnamed: C26.1, R57.2
unnamed: C27.1, R58.2
unnamed: C28.1, R59.2
unnamed: C29.1, R60.2
unnamed: C30.1, R61.2
unnamed: C31.1, R62.2
unnamed: D1.3, F1.2, RV1.1
unnamed: D2.2, R12.2
unnamed: D3.2, R15.2
unnamed: D4.2, R16.1
unnamed: D5.2, K1.1, Q3.3
unnamed: D6.1, R20.2
unnamed: D7.2, K2.1, Q4.3
unnamed: D8.1, R21.2
unnamed: D9.2, K3.1, Q5.3
unnamed: D10.1, R22.2
unnamed: D11.1, R23.1
unnamed: D12.1, R24.1
unnamed: D13.1, R25.1
unnamed: D14.1, R26.1
unnamed: D15.1, R27.1
unnamed: D16.1, R28.1
unnamed: D17.1, R29.1
unnamed: D18.1, R30.1
unnamed: F1.1, J2.2, J2.4, J2.6, J2.8
unnamed: J1.1, J2.1
unnamed: J4.2, JP6.1
unnamed: J4.3, JP4.2
unnamed: J5.6, JP7.1
unnamed: JP9.2, U3.4
unnamed: JP12.2, U5.4
unnamed: JP15.2, U7.5
unnamed: Q6.3, R47.1, U9.4
unnamed: Q7.3, R48.1, U10.4
unnamed: Q8.3, R49.1, U11.4
unnamed: Q9.3, R50.1, U12.4
unnamed: Q10.3, R51.1, U13.4
unnamed: Q11.3, R52.1, U14.4
unnamed: Q12.3, R53.1, U15.4
unnamed: Q13.3, R54.1, U16.4
unnamed: R10.2, R11.1, U3.5
unnamed: R31.1, U9.2
unnamed: R32.1, U10.2
unnamed: R33.1, U11.2
unnamed: R34.1, U12.2
unnamed: R35.1, U13.2
unnamed: R36.1, U14.2
unnamed: R37.1, U15.2
unnamed: R38.1, U16.2
unnamed: R39.2, U9.6
unnamed: R40.2, U10.6
unnamed: R41.2, U11.6
unnamed: R42.2, U12.6
unnamed: R43.2, U13.6
unnamed: R44.2, U14.6
unnamed: R45.2, U15.6
unnamed: R46.2, U16.6

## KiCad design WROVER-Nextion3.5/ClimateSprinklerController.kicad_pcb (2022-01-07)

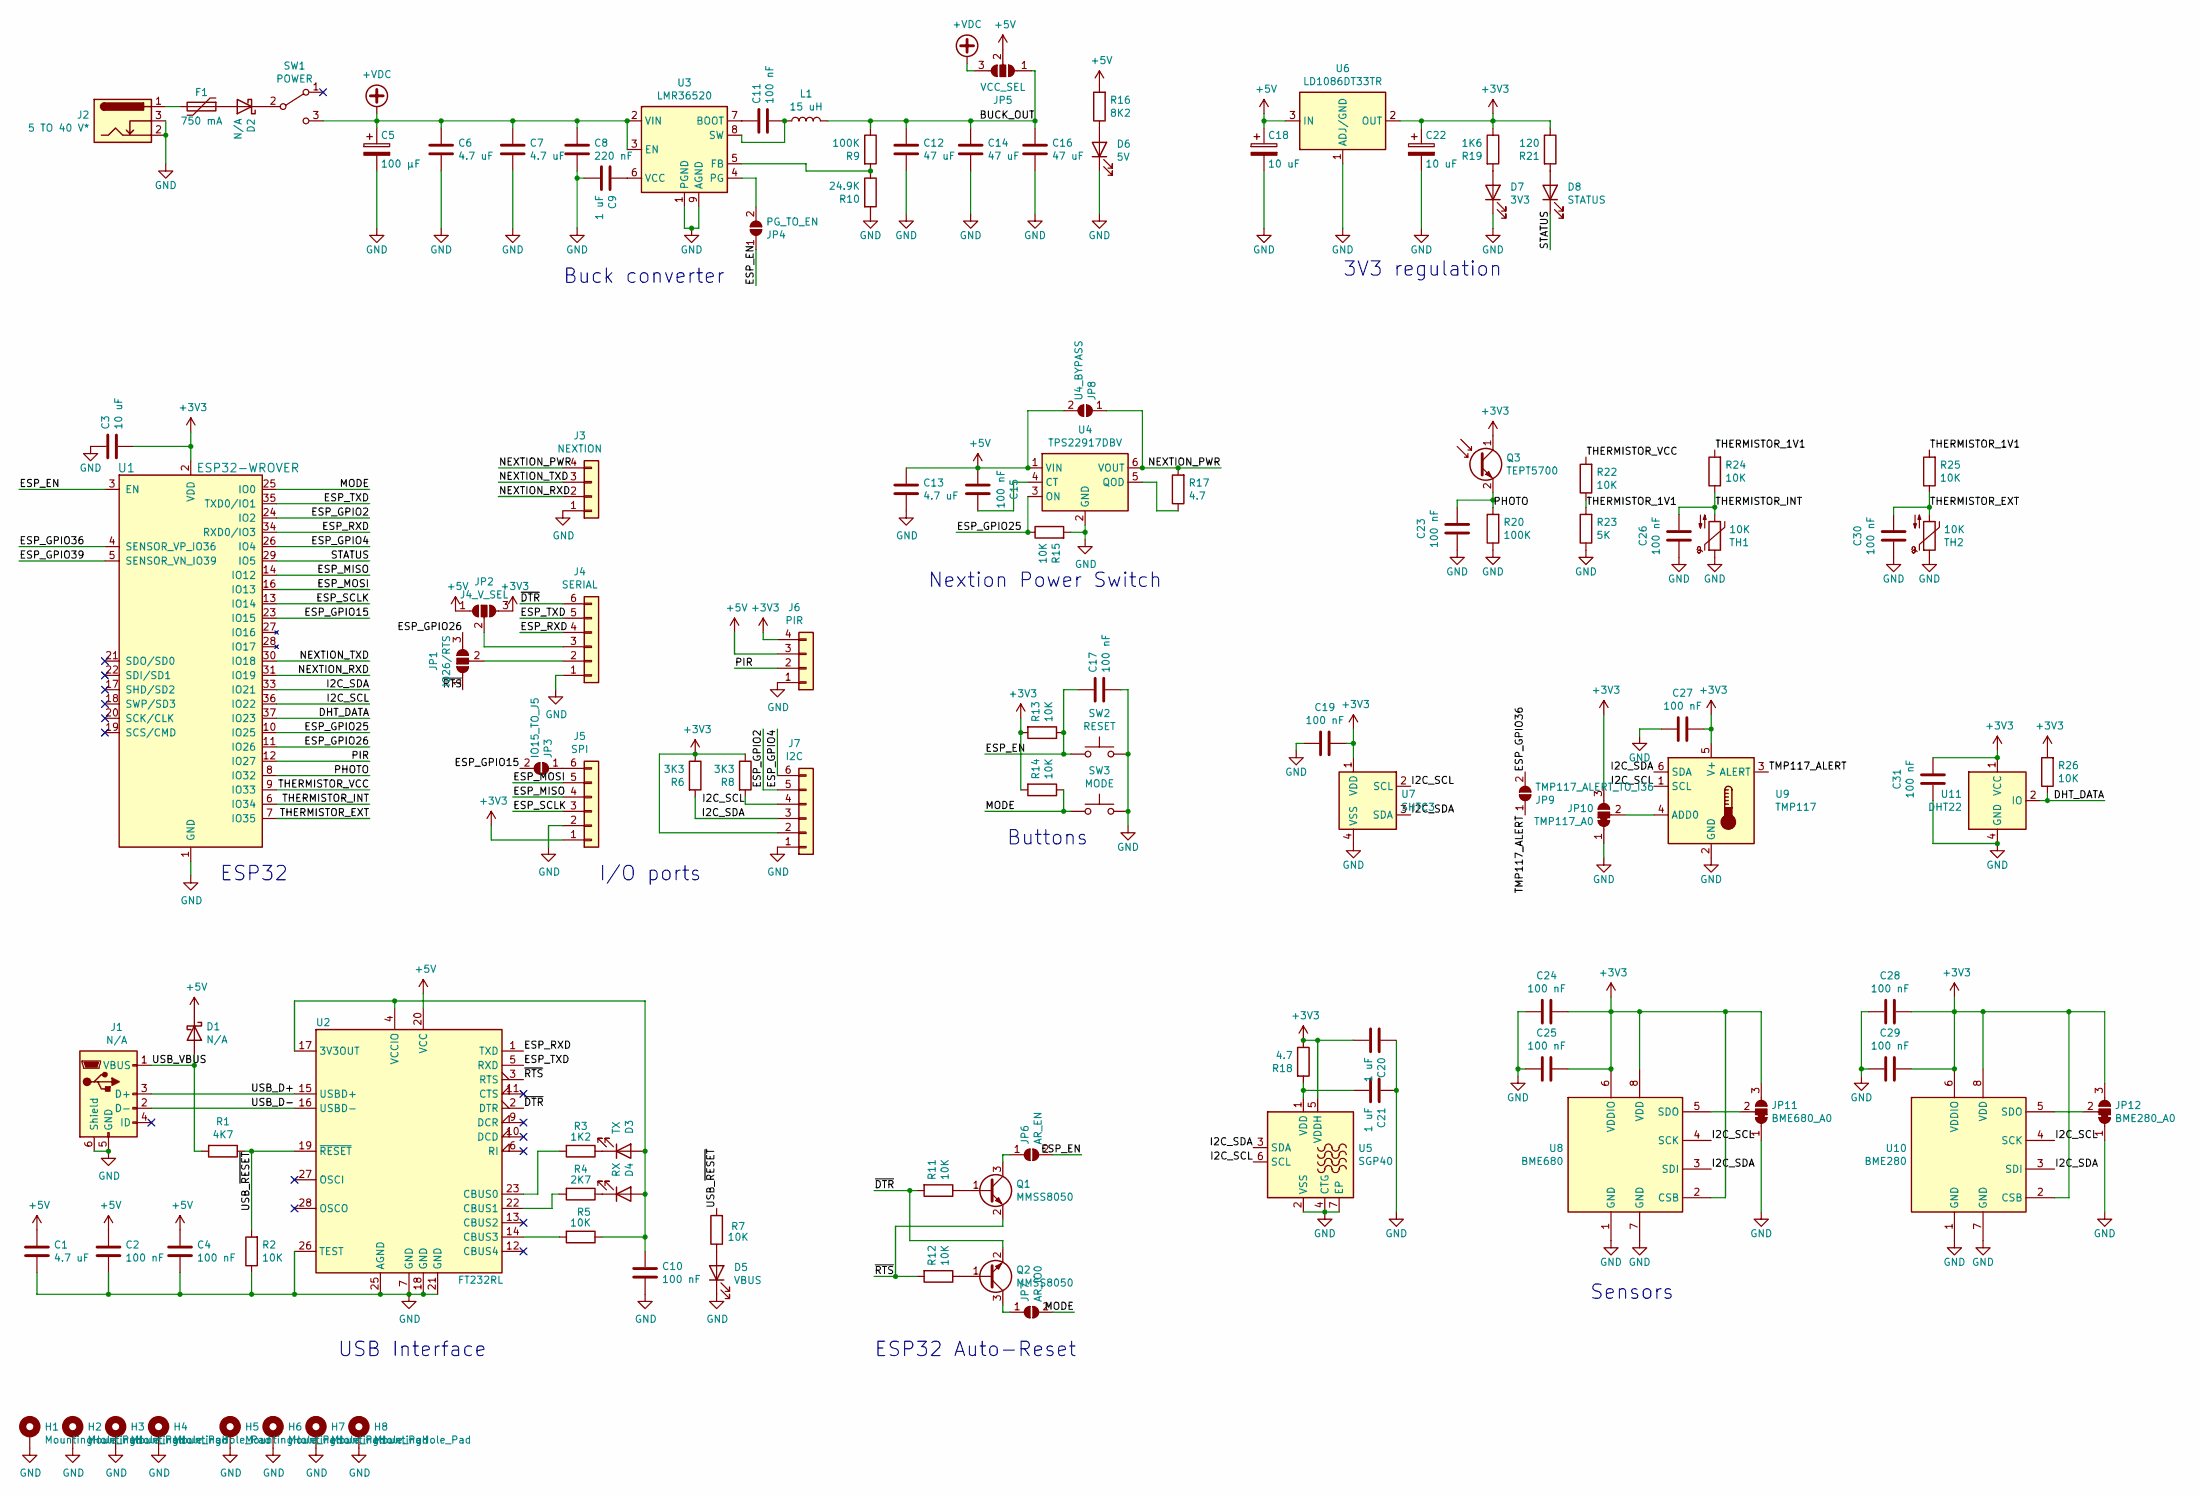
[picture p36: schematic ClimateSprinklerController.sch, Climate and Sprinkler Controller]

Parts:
C1, C6, C7, C13: 4.7 uF; C_0805_2012Metric; MPN1 C2012X5R1H475K125AB
C2, C4, C10, C11, C15, C17, C19, C23, C24, C25, C26, C27, C28, C29, C30, C31: 100 nF; C_0805_2012Metric; MPN1 CC0805KRX7R7BB104
C3: 10 uF; C_0805_2012Metric; MPN1 C2012X5R1V106K085AC
C5: 100 µF; CP_Elec_8x10; MPN1 25SVF100M
C8: 220 nF; C_0805_2012Metric; MPN1 C2012X5R1H224K125AA
C9, C20, C21: 1 uF; C_0805_2012Metric; MPN1 C0805C105K4RACTU
C12, C14, C16: 47 uF; C_1210_3225Metric; MPN1 GRM32ER61C476KE15L
C18, C22: 10 uF; CP_Elec_5x5.8; MPN1 EEE-HP0J100R
D1, D2: N/A; D_SOD-123F; MPN1 MBR230S1F-7
D3: TX; LED_1206_3216Metric_ReverseMount_Hole1.8x2.4mm; MPN1 APTL3216QBC/D
D4: RX; LED_1206_3216Metric_ReverseMount_Hole1.8x2.4mm; MPN1 APTL3216SURCK
D5: VBUS; LED_1206_3216Metric_ReverseMount_Hole1.8x2.4mm; MPN1 APTL3216ZGC
D6: 5V; LED_1206_3216Metric_ReverseMount_Hole1.8x2.4mm; MPN1 597-6901-607F
D7: 3V3; LED_1206_3216Metric_ReverseMount_Hole1.8x2.4mm; MPN1 597-6901-607F
D8: STATUS; LED_1206_3216Metric_ReverseMount_Hole1.8x2.4mm; MPN1 APTL3216SECK
F1: 750 mA; Fuse_2920_7451Metric; MPN1 2920L075
H1, H2, H3, H4: MountingHole_Pad; MountingHole_3.2mm_M3_Pad_Via; MPN1 N/A
H5, H6, H7, H8: MountingHole_Pad; MountingHole_3.2mm_M3_DIN965_Pad; MPN1 N/A
J1: N/A; USB_Micro-B_Molex-105017-0001; MPN1 105017-0001
J2: 5 TO 40 V*; BarrelJack_Horizontal; MPN1 694106301002
J3: NEXTION; PinSocket_1x04_P2.54mm_Vertical; MPN1 N/A
J4: SERIAL; PinSocket_1x06_P2.54mm_Vertical; MPN1 N/A
J5: SPI; PinSocket_1x06_P2.54mm_Vertical; MPN1 N/A
J6: PIR; PinSocket_1x04_P2.54mm_Vertical; MPN1 N/A
J7: I2C; PinSocket_1x06_P2.54mm_Vertical; MPN1 N/A
JP1: IO26/RTS; SolderJumper-3_P1.3mm_Open_RoundedPad1.0x1.5mm; MPN1 N/A
JP2: J4_V_SEL; SolderJumper-3_P1.3mm_Open_RoundedPad1.0x1.5mm; MPN1 N/A
JP3: IO15_TO_J5; SolderJumper-2_P1.3mm_Open_RoundedPad1.0x1.5mm; MPN1 N/A
JP4: PG_TO_EN; SolderJumper-2_P1.3mm_Open_RoundedPad1.0x1.5mm; MPN1 N/A
JP5: VCC_SEL; SolderJumper-3_P1.3mm_Open_RoundedPad1.0x1.5mm; MPN1 N/A
JP6: AR_EN; SolderJumper-2_P1.3mm_Open_RoundedPad1.0x1.5mm; MPN1 N/A
JP7: AR_IO0; SolderJumper-2_P1.3mm_Open_RoundedPad1.0x1.5mm; MPN1 N/A
JP8: U4_BYPASS; SolderJumper-2_P1.3mm_Open_RoundedPad1.0x1.5mm; MPN1 N/A
JP9: TMP117_ALERT_TO_I36; SolderJumper-2_P1.3mm_Open_RoundedPad1.0x1.5mm; MPN1 N/A
JP10: TMP117_A0; SolderJumper-3_P1.3mm_Bridged12_RoundedPad1.0x1.5mm; MPN1 N/A
JP11: BME680_A0; SolderJumper-3_P1.3mm_Bridged12_RoundedPad1.0x1.5mm; MPN1 N/A
JP12: BME280_A0; SolderJumper-3_P1.3mm_Bridged12_RoundedPad1.0x1.5mm; MPN1 N/A
L1: 15 uH; L_Wuerth_WE-PD-Typ-LS; MPN1 7447709150
Q1, Q2: MMSS8050; SOT-23; MPN1 MMSS8050
Q3: TEPT5700; LED_D5.0mm_Clear; MPN1 TEPT5700
R1: 4K7; R_0805_2012Metric_Pad1.20x1.40mm_HandSolder; MPN1 RT0805FRE074K7L
R2, R5, R7, R11, R12, R13, R14, R15, R22, R24, R25, R26: 10K; R_0805_2012Metric_Pad1.20x1.40mm_HandSolder; MPN1 RC0805FR-0710KL
R3: 1K2; R_0805_2012Metric_Pad1.20x1.40mm_HandSolder; MPN1 RT0805FRE072K7L
R4: 2K7; R_0805_2012Metric_Pad1.20x1.40mm_HandSolder; MPN1 RT0805FRE072K7L
R6, R8: 3K3; R_0805_2012Metric_Pad1.20x1.40mm_HandSolder; MPN1 RT0805FRE073K3L
R9, R20: 100K; R_0805_2012Metric_Pad1.20x1.40mm_HandSolder; MPN1 RC0805FR-07100KL
R10: 24.9K; R_0805_2012Metric_Pad1.20x1.40mm_HandSolder; MPN1 RT0805FRE0724K9L
R16: 8K2; R_0805_2012Metric_Pad1.20x1.40mm_HandSolder; MPN1 RT0805FRE078K2L
R17, R18: 4.7; R_0805_2012Metric_Pad1.20x1.40mm_HandSolder; MPN1 RC0805FR-074R7L
R19: 1K6; R_0805_2012Metric_Pad1.20x1.40mm_HandSolder; MPN1 RT0805FRE071K6L
R21: 120; R_0805_2012Metric_Pad1.20x1.40mm_HandSolder; MPN1 RT0805FRE07120RL
R23: 5K; R_0805_2012Metric_Pad1.20x1.40mm_HandSolder; MPN1 CRCW08055K00JNTA
SW1: POWER; SW_Push_1P2T_Vertical_E-Switch_800UDP8P1A1M6; MPN1 48BFSP1M6QT
SW2: RESET; SW_Tactile_SPST_Angled_PTS645Vx58-2LFS; MPN1 PTS645VK582LFS
SW3: MODE; SW_Tactile_SPST_Angled_PTS645Vx58-2LFS; MPN1 PTS645VK582LFS
TH1, TH2: 10K; PinSocket_1x02_P2.54mm_Vertical; MPN1 NXFT15XH103FA2B100
U1: ESP32-WROVER; MPN1 ESP32-WROVER
U2: FT232RL; SSOP-28_5.3x10.2mm_P0.65mm; MPN1 FT232RL
U3: LMR36520; Texas_HSOP-8-1EP_3.9x4.9mm_P1.27mm_ThermalVias; MPN1 LMR36520ADDAR
U4: TPS22917DBV; SOT-23-6; MPN1 TPS22917DBV
U5: SGP40; DFN-6-1EP_2.44x2.44mm_P0.8mm_EP1.25x1.7mm; MPN1 SGP40
U6: LD1086DT33TR; TO-252-2; MPN1 LD1086DT33TR
U7: SHTC3; AMS_QFN-4-1EP_2x2mm_P0.95mm_EP0.7x1.6mm; MPN1 SHTC3
U8: BME680; Bosch_LGA-8_3x3mm_P0.8mm_ClockwisePinNumbering; MPN1 BME680
U9: TMP117; WSON-6-1EP_2x2mm_P0.65mm_EP1x1.6mm; MPN1 TMP117MAIDRVR
U10: BME280; Bosch_LGA-8_2.5x2.5mm_P0.65mm_ClockwisePinNumbering; MPN1 BME280
U11: DHT22; PinSocket_1x04_P2.54mm_Vertical; MPN1 DHT22

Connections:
+3V3: C3.2, C19.1, C20.2, C22.1, C24.1, C25.1, C27.1, C28.1, C29.1, C31.1, J5.1, J6.4, J7.2, JP2.3 (B), JP10.3 (B), JP11.3 (B), JP12.3 (B), Q3.1 (C), R6.1, R8.1, R13.2, R14.2, R18.1, R19.1, R21.1, R26.2, U1.2 (VDD), U5.5 (VDDH), U6.2 (OUT), U7.1 (VDD), U8.2 (CSB), U8.6 (VDDIO), U8.8 (VDD), U9.5 (V+), U10.2 (CSB), U10.6 (VDDIO), U10.8 (VDD), U11.1 (VCC)
+5V: C1.1, C2.1, C4.1, C13.1, C15.2, C18.1, D1.1 (K), J6.3, JP2.1 (A), JP5.2 (C), JP8.2 (B), R16.2, U2.20 (VCC), U4.1 (VIN), U6.3 (IN)
+VDC: C5.1, C6.1, C7.1, C8.1, JP5.3 (B), SW1.3 (C), U3.2 (VIN), U3.3 (EN)
/BUCK_OUT: C12.1, C14.1, C16.1, JP5.1 (A), L1.2, R9.1
/DHT_DATA: R26.1, U1.37 (IO23), U11.2 (IO)
/ESP_EN: C17.1, JP4.1 (A), JP6.2 (B), R13.1, SW2.2, U1.3 (EN)
/ESP_GPIO2: J7.5, U1.24 (IO2)
/ESP_GPIO4: J7.6, U1.26 (IO4)
/ESP_GPIO15: JP3.2 (B), U1.23 (IO15)
/ESP_GPIO25: R15.1, U1.10 (IO25), U4.3 (ON)
/ESP_GPIO26: JP1.3 (B), U1.11 (IO26)
/ESP_GPIO36: JP9.2 (B), U1.4 (SENSOR_VP_IO36)
/ESP_MISO: J5.4, U1.14 (IO12)
/ESP_MOSI: J5.5, U1.16 (IO13)
/ESP_RXD: J4.4, U1.34 (RXD0/IO3), U2.1 (TXD)
/ESP_SCLK: J5.3, U1.13 (IO14)
/ESP_TXD: J4.5, U1.35 (TXD0/IO1), U2.5 (RXD)
/I2C_SCL: J7.4, R8.2, U1.36 (IO22), U5.6 (SCL), U7.2 (SCL), U8.4 (SCK), U9.1 (SCL), U10.4 (SCK)
/I2C_SDA: J7.3, R6.2, U1.33 (IO21), U5.3 (SDA), U7.3 (SDA), U8.3 (SDI), U9.6 (SDA), U10.3 (SDI)
/MODE: JP7.2 (B), R14.1, SW3.1, U1.25 (IO0)
/NEXTION_PWR: J3.4, JP8.1 (A), R17.2, U4.6 (VOUT)
/NEXTION_RXD: J3.2, U1.31 (IO19)
/NEXTION_TXD: J3.3, U1.30 (IO18)
/PHOTO: C23.1, Q3.2 (E), R20.2, U1.8 (IO32)
/PIR: J6.2, U1.12 (IO27)
/STATUS: D8.1 (K), U1.29 (IO5)
/THERMISTOR_1V1: R22.1, R23.2, R24.2, R25.2
/THERMISTOR_EXT: C30.1, R25.1, TH2.2, U1.7 (IO35)
/THERMISTOR_INT: C26.1, R24.1, TH1.2, U1.6 (IO34)
/THERMISTOR_VCC: R22.2, U1.9 (IO33)
/TMP117_ALERT: JP9.1 (A), U9.3 (ALERT)
/USB_D+: J1.3 (D+), U2.15 (USBD+)
/USB_D-: J1.2 (D-), U2.16 (USBD-)
/USB_VBUS: D1.2 (A), J1.1 (VBUS), R1.2
/USB_~RESET: R1.1, R2.2, R7.2, U2.19 (~RESET~)
/~DTR: J4.6, Q2.2 (E), R11.2, U2.2 (DTR)
/~RTS: JP1.1 (A), Q1.2 (E), R12.2, U2.3 (RTS)
GND: C1.2, C2.2, C3.1, C4.2, C5.2, C6.2, C7.2, C8.2, C9.2, C10.2, C12.2, C13.2, C14.2, C16.2, C17.2, C18.2, C19.2, C20.1, C21.1, C22.2, C23.2, C24.2, C25.2, C26.2, C27.2, C28.2, C29.2, C30.2, C31.2, D5.1 (K), D6.1 (K), D7.1 (K), H1.1, H2.1, H3.1, H4.1, H5.1, H6.1, H7.1, H8.1, J1.5 (GND), J1.6 (Shield), J2.2, J2.3, J3.1, J4.1, J5.2, J6.1, J7.1, JP10.1 (A), JP11.1 (A), JP12.1 (A), R2.1, R10.2, R15.2, R20.1, R23.1, SW2.1, SW3.2, TH1.1, TH2.1, U1.1 (GND), U1.15 (GND), U1.38 (GND), U1.39 (GND), U2.7 (GND), U2.18 (GND), U2.21 (GND), U2.25 (AGND), U2.26 (TEST), U3.1 (PGND), U3.9 (AGND), U4.2 (GND), U5.2 (VSS), U5.4 (CTG), U5.7 (EP), U6.1 (ADJ/GND), U7.4 (VSS), U8.1 (GND), U8.7 (GND), U9.2 (GND), U10.1 (GND), U10.7 (GND), U11.4 (GND)
unnamed: C9.1, U3.6 (VCC)
unnamed: C10.1, D3.2 (A), D4.2 (A), R5.1, U2.4 (VCCIO), U2.17 (3V3OUT)
unnamed: C11.1, U3.7 (BOOT)
unnamed: C11.2, L1.1, U3.8 (SW)
unnamed: C15.1, U4.4 (CT)
unnamed: C21.2, R18.2, U5.1 (VDD)
unnamed: D2.1 (K), SW1.2 (B)
unnamed: D2.2 (A), F1.1
unnamed: D3.1 (K), R3.1
unnamed: D4.1 (K), R4.1
unnamed: D5.2 (A), R7.1
unnamed: D6.2 (A), R16.1
unnamed: D7.2 (A), R19.2
unnamed: D8.2 (A), R21.2
unnamed: F1.2, J2.1
unnamed: J4.2, JP1.2 (C)
unnamed: J4.3, JP2.2 (C)
unnamed: J5.6, JP3.1 (A)
unnamed: JP4.2 (B), U3.4 (PG)
unnamed: JP6.1 (A), Q1.3 (C)
unnamed: JP7.1 (A), Q2.3 (C)
unnamed: JP10.2 (C), U9.4 (ADD0)
unnamed: JP11.2 (C), U8.5 (SDO)
unnamed: JP12.2 (C), U10.5 (SDO)
unnamed: Q1.1 (B), R11.1
unnamed: Q2.1 (B), R12.1
unnamed: R3.2, U2.23 (CBUS0)
unnamed: R4.2, U2.22 (CBUS1)
unnamed: R5.2, U2.14 (CBUS3)
unnamed: R9.2, R10.1, U3.5 (FB)
unnamed: R17.1, U4.5 (QOD)

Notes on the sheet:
I/O ports
ESP32
Buttons
Sensors
ESP32 Auto-Reset
USB Interface
Nextion Power Switch
3V3 regulation
Buck converter

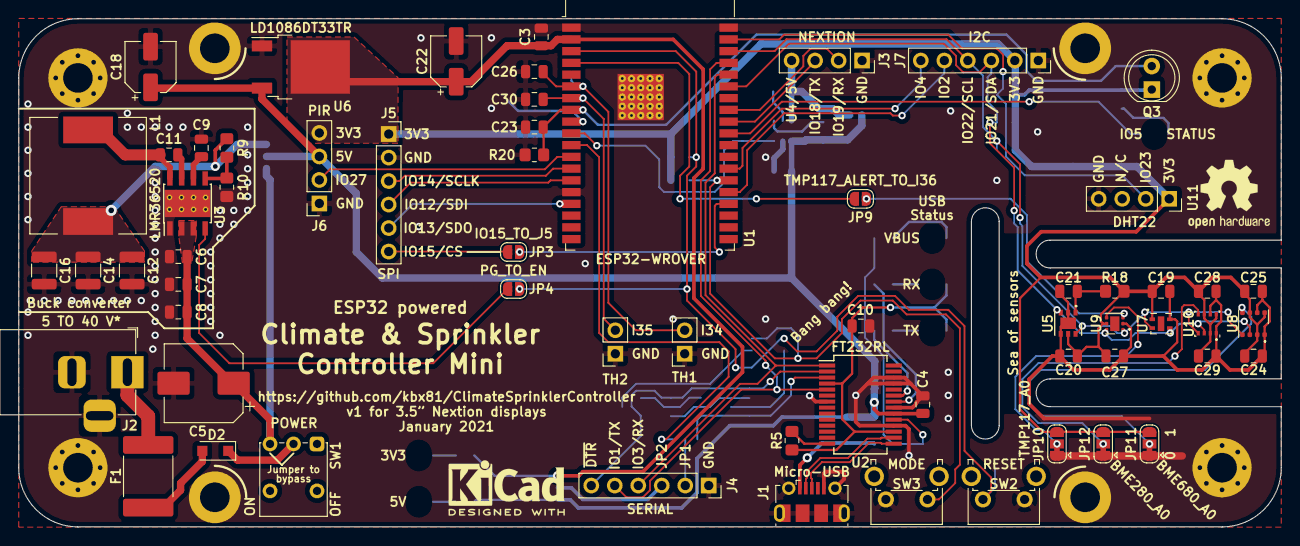
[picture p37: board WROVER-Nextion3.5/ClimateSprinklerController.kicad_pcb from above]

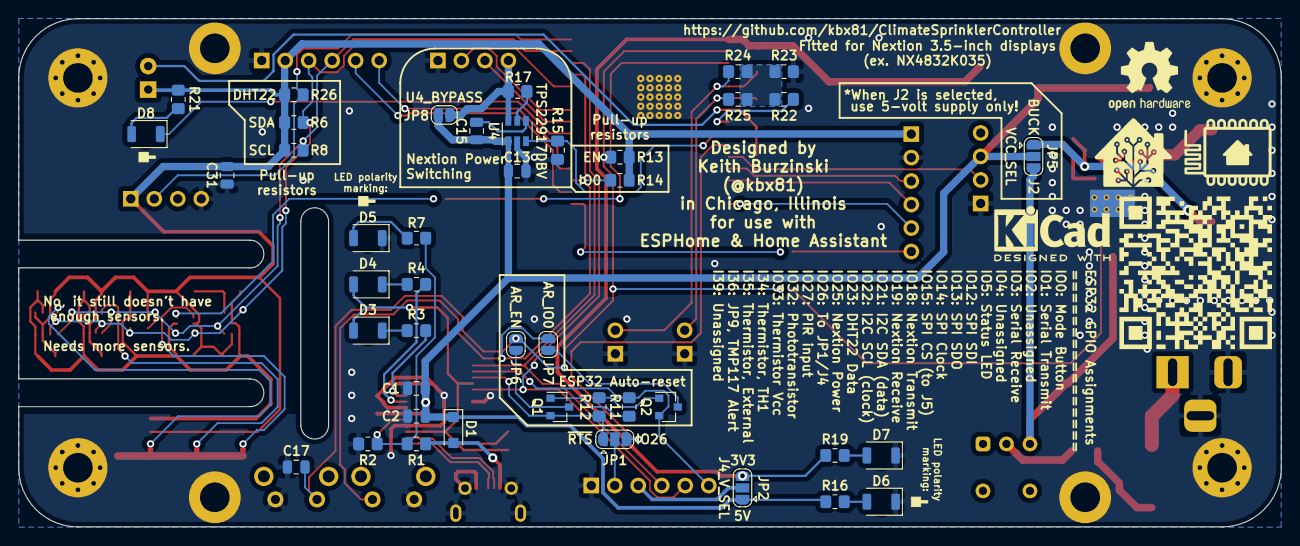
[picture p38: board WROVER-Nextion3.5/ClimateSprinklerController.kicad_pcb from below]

Board: 2 copper layers, 136.5 x 54.9 mm, 114 parts (44 on the bottom side), 69 nets.

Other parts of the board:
QR*****: ClimateSprinklerControllerQR

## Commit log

2021-01-25 Nextion PCBs initial commit
    [ClimateSprinklerController-B_Cu.gbr, ClimateSprinklerController-B_Mask.gbr, ClimateSprinklerController-B_Paste.gbr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]
2021-01-25 Nextion PCBs tweak
    [ClimateSprinklerController-B_Cu.gbr, ClimateSprinklerController-B_Mask.gbr, ClimateSprinklerController-B_Paste.gbr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]
2021-01-31 TX+RX LEDs were backwards...oops
    [ClimateSprinklerController-B_Cu.gbr, ClimateSprinklerController-B_Mask.gbr, ClimateSprinklerController-B_Paste.gbr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]
2022-01-07 Doc updates, new images, new enclosures, regenerate gerbers
    [BackCover.stl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]
